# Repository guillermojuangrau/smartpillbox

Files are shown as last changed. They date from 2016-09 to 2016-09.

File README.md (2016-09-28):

# Project Title

Smart pillbox concept completed as a final project for Telecommunications Engineering Degree

## Summary of the project

Conception, design and creation of a smart pillbox (physical parts, hardware and software) as well as production of a 3D printed open-source physical wireless prototype able to automatically sort and dispense pills to dependent polymedicated patients reducing medication errors and improving medical adherence.

### Contents of the project

Project is intended to be a prototype for a smart pillbox therefore in this project there will be several subcontents regarding hardware, software or electronics.
Below there is a list of the different contents included:

1.Smart_pillbox_project_Guillermo_de_Juan.pdf - Project thesis and documentation which was presented in the final project presentation
2.Code - Code to be run in the pillbox's processor.
3.Body - Files of the 3D parts of the pillbox to be printed in 3D.
4.Schematics - Files of the schematics.

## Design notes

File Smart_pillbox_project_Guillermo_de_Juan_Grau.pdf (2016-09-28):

## ESCUELA POLITÉCNICA SUPERIOR UNIVERSIDAD CARLOS III DE MADRID

## GRADO EN INGENIERÍA EN TECNOLOGÍAS DE TELECOMUNICACIÓN

–

## DEGREE IN TELECOMMUNICATIONS TECHNOLOGY ENGINEERING

## BACHELOR THESIS – TRABAJO DE FIN DE GRADO

# SMART PILL DISPENSER FOR DEPENDENT PEOPLE

Author: Guillermo de Juan Grau Tutor: Daniel Díaz Sánchez September 2015

## ACKNOWLEDGEMENTS

In this section I would like to publicly thank everyone who has contributed in making possible for me to reach this point in my life.

To my parents, without whom I could not be the person I am today, for making me a better person since the day I was born.

To my sisters, for being always there when I need them.

To Ana, for every one of those moments in which I needed all the support and love in the world and she gave me much more than that.

To Gonzalo for those endless nights of studying, as it has finally been worth it.

To Rafa, for all he taught me the moments we spent together.

To Sara, Irene, Alicia and Dani for being the main drives of my life.

And to everyone who has helped in one or another way to make this come true.

Thank you, from the bottom of my heart.

## INDEX

6.2 | Printing software | 81
6.3 | Printing in 3D | 82
6.4 | Printed parts | 84
6.5 | Pillbox assembly and encountered problems | 86
7 | Testing the pillbox | 88
7.1 | Miscellaneous tests | 89
7.2 | Tests for the default stage | 90
7.3 | Tests for the management stage | 91
7.4 | Tests for the dispensing stage | 94
8 | Planning and budget | 96
8.1 | Planning | 96
8.2 | Budget | 99
9 | Conclusions and future work | 100
10 | References | 102
11 | Annex | 106

## CHART INDEX

## FIGURE INDEX

Figure 37: A cube is overlapped with the created part to make an entry hole in the cylinder.. 49 Figure 38: After the cube has been substracted from the cylinder the entry hole is created.... 50

Figure 48: Some of the electronic components which have been used to test and create the

Figure 50: Funduino along with the tools used to solder the necessary pins onto the board ... 57

Figure 57: Connection breadboard schematic of the speaker, LEDs, switch and button

Figure 70: Prusa i3 steel used to print the pillbox parts once assembled and functional, already

Figure 73: Example of printing a cone in a standing position and in a side position, the standing

Figure 75: Parts with the necessary quality which will be used to assemble the prototype: pill

## ABSTRACT

Many medical errors are due to the fact that people in charge of patient or elder’s medication have to deal with sorting huge amounts of pills each day. This paper consists on the conception, design and creation of a pillbox prototype intended to solve this deficiency in the medical area as it has the ability of sorting out the pills by itself as well as many other advanced features, with this device being intended to be used by hospitals or retirement homes. For the design of this device open-source based technologies will be used when possible including 3D design software and software IDE, and the prototype will be created using 3D printed plastic parts.

## 1 INTRODUCTION

### 1.1 INTRODUCTION

Medicine hasn’t always been the precise science which we know nowadays, in fact, throughout history the vast majority of maladies and afflictions would have resulted in probable death. Fortunately medicine has experienced a great development in the last century, resulting in an increased life expectancy and the possibility to cure a great quantity of diseases and health disorders.

Pills are one of the pillars of medicine, being used as direct treatments of some sort of illness as to assuring some medical condition remains stable (people with organ transplants or patients suffering from a chronic disease such as VIH).

### 1.2 PROBLEM STATEMENT

As pills have taken such an important role in everyday life there has been the past years an increase in the number of medical neglect cases related to incorrect medication given to patients, such as the case of the nurse who gave a patient a paralytic instead of an antacid that was prescribed by the doctor, causing the patient’s death [1]. After seeing so many of these cases it is evidently crucial that the correct pill is taken by the correct person at the correct time, otherwise taking an incorrect one or not taking one at all may expose the patient to several dangerous situations, ranging from mild health issues up to death.

Other cases of wrong pills being ingested by patients are caused by patients themselves, especially at an old age. As people grow old the human body tends to malfunction and the number of pills the average person has to take when certain age is reached greatly increases, were, according to a 2008 study published in the Journal of the American Medical Association, more than 40 percent of Americans age 65 and older take five medications a day [2]. Usually they are a wide range of different pills an elderly has to take at different times. Keeping track of taking the right pill at the right moment each day can become a challenging experience for the elderly, as it is not as easy as it could be for a younger person. This fact is easily explained when we understand that many of the abilities such as sight, memory or logical capabilities tend to decrease in a proportional way to age once human beings have entered old age, making it difficult for them to remember which pill to take at the correct time, remembering to take them or confusing one pill with another as the person may not be able to distinguish one from another thanks to their decreased sight as well as the similarity in the pills forms and colours. This problem will most surely be a cause for concern for the people surrounding the pill-taker, as not taking a pill at the correct time can cause severe problems (such as organ rejection in a patient with organ transplant or heart attack in patients suffering from grave heart conditions).

On the other hand several problems related to the high amount of pills nowadays are prescribed to patients are found in hospitals or in retirement homes. In these places on of the main jobs is to give out to its patient the correct pills. Managing, sorting and giving out the pills to each one of the patients can sometimes have a high chance of error, with a patient or resident receiving one or more incorrect pills.

Finally there are situation where taking an incorrect amount of pills is a matter of the patient’s inexperience and/or ignorance. No matter the cause, it has been proven that there is a significant risk of people ending up swallowing the incorrect medication or dose.

### 1.3 OBJECTIVES

The main objective of this project will be to solve the aforementioned problems by designing and synthesize a tool which will enable the owner to track every pillf to ingest in an easy and simple way requiring no training or complex learning from their side in order to operate the device. This device will be an intelligent pill dispenser.

The pill dispenser will be designed to prevent errors in hospitals and retirement homes where many pills have to be given daily to each one of the patients, each patient owning a device will not only drastically reduce the chances of errors occurring but also well optimize and speed up work for the caretakers/nurses by allowing the device to take care of pill management for them and freeing the time slot usually dedicated to that.

This device is intended to log the pill name, number of pills and hours at which each pill is actually taken versus the time it should have been taken. Nowadays there has been an increasing awareness as the number of pills prescribed to elder people, stating that so many pills may have negative effects on the patient’s health. [3] [4] The pillbox’s logs will help gather data concerning this matter.

There is a need to ensure the device is wirelessly connected so device management (defining the hours when a particular pill must be taken, number of pills in each compartment, etc…) as well as possibility of emitting warnings to the owner’s relatives or nurses if needed (such as the patient not taking pills).

In essence, the device will have to be a wireless electronic apparatus, having special attention to make it very precise as an error could prove fatal.

### 1.4 REGULATORY FRAMEWORK

The pillbox is a device which helps handling patient’s medication.For this reason the process in which to implement the pillbox in the selected organizations (mainly hospitals and retirement homes as already mentioned) will be a process similar to the one medications have to follow when being implemented in the general market.

Chart 1 shown below shows the different level through which the product will have to traverse after being implemented in public institutions. [5]

Level 1: Medication agencies EMEA (European Medicines Evaluation Agency) execute the authorization registry report in which they authorize the product commercialization based on demographic risk versus benefit study.
Level 2: The Spanish Dirección General de Farmacia y Productos Sanitarios del Ministerio de Sanidad fix the product’s Price as well as the government’s funding conditions if any.
Level 3: The Health Counselors (Consejerias de Sanidad) in each of Spain’s autonomous communities will be the ones funding the use of the product.
Level 4: Each one of the sanitary institutions will be the ones to value if the product if worth the implementation depending on the product’s value and necessity inside the institution.
Chart 1: Regulatory framework leves for a new farmaceutical drug or related

Before the product traverses through any of the levels shown in the table it will be necessary to study if the invention patented in the Spanish territory in the OEPM (Oficina Española de Patentes y Marcas) to stop any plagiarism from happening.

### 1.5 DOCUMENT STRUCTURE

In this section the structure this document follows will be detailed along with a brief explanation of each one of the different sections:

Introduction

In this section the general aims of this document is provided alongside the proposed solution and the regulatory framework which concerns the product.

State of the art

In this section different technologies similar to the one being designed are analysed as well as the different existing technologies which will help implement the pillbox.

Product design specification

This section details the different requirements and features the pillbox must possess in order to achieve successfully the aim intended in this document.

Conceptual design

In the conceptual design section an early draft of the pillbox’s behaviour is outlined as well as different draft drawings of how the pillbox could look like. These draft drawings will be later used to design the final pillbox.

Pillbox design

In this section the pillbox is designed. The pillbox functionality is divided into modules and a simplified schematic is produced. The different modules are detailed from an operational point of view and changes to the original design are also outlined. The 3D parts are designed and detailed alongside with the pillbox’s electronic circuit schematics and the code needed for the pillbox to successfully function.

Synthesizing the pillbox

This section deals on how the prototype is converted from digital to a real model. The chosen 3D technology which will be used to print the pillbox is explained along with the procedure to follow an encountered problems while achieving that.

Finally the pillbox’s creation and assembly is also covered.

Testing the pillbox

This section shows the different tests applied to the pillbox to ensure complete functionality and the changes the pillbox has to undergo to successfully pass the failed tests.

Planning and budget

This section details the planification followed for the completion of this project and the hours dedicated to each tasks as well as the necessary budget to cover the project.

Conclusions

This section covers the future improvements that could be done to the pillbox in order to optimize it and increment the number of features it presents as well as to correct errors the actual prototype possesses.

The project as a whole is reflected upon once it has been finished and the several conclusions drawn out of it are exposed.

References

The sources used and cited throughout this project are listed in this section.

Annex

Additional documentation such as high detail schematics of the printed parts are included in this section.

## 2 STATE OF THE ART

### 2.1 INTRODUCTION

Throughout this section a detailed a thorough investigation of products similar to the one developed in this project will be carried out so that a learning process is achieved in order to avoid committing common errors and flaws as well as ensuring that this project offers and outsmarts every other product in the market nowadays.

In second place the different available technologies needed for the creation of this product will be examined in order to pick the optimal ones which will be finally used to make it a reality.

### 2.2 SMART PILL BOXES

Despite the short time pill boxes have been in the market many different models can already be found with a wide range of different functionalities and intended for disparate uses and contexts. Most prominent ones will be cited.

### 2.2.1 AdhereTech’s smart pill bottle

AdhereTech smart pill bottle [6] consists on a plastic bottle in which to store the pills and some circuitry which allows for the bottle how many times the pillbox is opened. It uses sensors for a precise measurement of remaining medication and can send messages, calls or notifications to patient if pill is not taken. Its main weak points are the impossibility of storing different pill types in one bottle as well as having a lack on information on how the pillbox can be managed, which may led to believe it will only be implemented at hospital-level. On figure 1 the pillbox is shown.

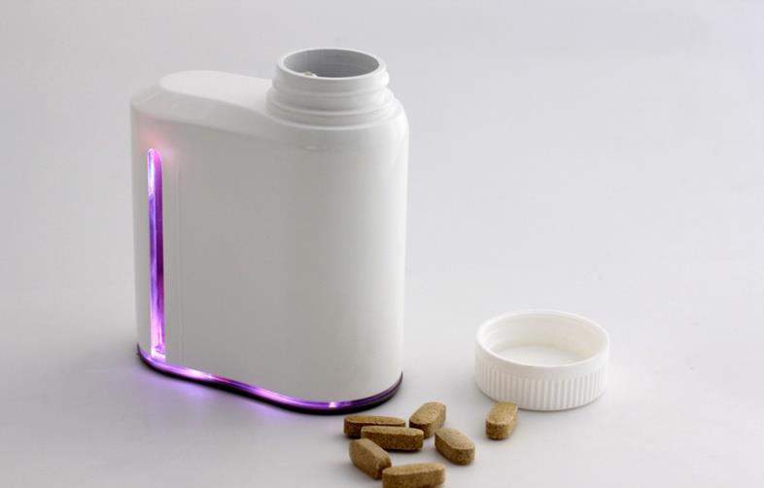
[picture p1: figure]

Figure 1: AdhereTech’s smart pill bottle

### 2.2.2 iMediPac

iMediPac [7] is an intelligent pillbox in which pills are sorted by each day in a disposable envelope which will be later inserted in the pillbox. Each day the pillbox lights up the compartment which has to be taken that day and the user breaks and retrieves the pills from inside the pillbox. If pills are not taken the pillbox alerts relatives with notifications. On the down side, the pillbox is very bulky of a huge size making it difficult for a person to carry it all day, while pills will probably have to be taken throughout the day. It also shows in the promotional videos a complex method of configuring personal data, which may lead to elderly people not being able to program it correctly. Finally it doesn’t solve the problem of pills complexity as nurses, pharmacists, etc… have to spend huge amounts of time preparing the dose for each day in the refill sheet as well as refills having to be constantly bought and refilled. Figure 2 shows the iMediPac pillbox with a refill loaded with pills.

[7]

Figure 2: iMediPac pillbox.

### 2.2.3 MemoBox

MemoBox [8] is a small pillbox with just one compartment in which many different pills can be stored. It possess a portable size and can track when the pillbox is forgotten at home. Whilst its simplicity can be very attractive it offers no more functionality than the one which could be achieved with a normal pillbox and a pill-reminder app installed in the phone. Figure 3 shows the MemoBox pillbox with different pills stored inside.

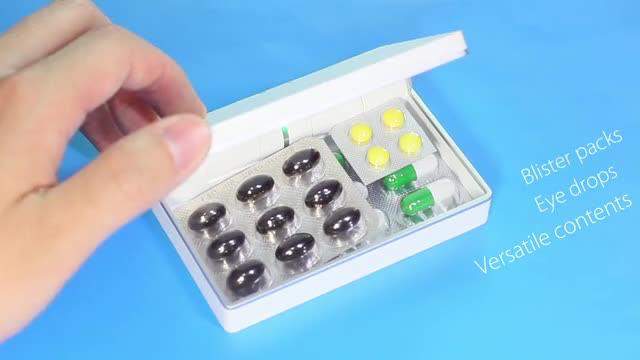
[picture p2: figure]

Figure 3: MemoBox pillbox

### 2.2.4 uBox

uBox [9] is a really small pillbox which can be easily carried by its user. It consists on a cylindrical structure with different compartments inside. It has a childproof lock and can alert user and relatives if pills are not taken. Different pills for each dose are stored in the same compartments, which may be its only inconvenient. Figure 4 is an actual photograph of the pillbox while Figure 5 shows an exploded view of the pillbox.

Figure 4: uBox pillbox

Figure 5: Exploded view of the uBox pillbox

### 2.2.5 GlowCap & GlowPacks

GlowCap [10] is a smart pillbottle lid which can attach to the normal pillbottle and comes with a wall plug device (GlowPack) which lights up each time the user has to take a pill. The pillbox lid has an interior button which can be pressed to directly order pills to the drugstore. This smart pillbox has many inconvenients:

- One cap per bottle of pills.
- Not portable as needs a wall plug-in.
- Elderly need to have computer knowledge in order to set it up.

- Pressing twice the button when pill box is near emptying places a call from your phone to the pharmacy, same thing could be achieved with speed-dial directly from the phone.
- As they are caps, only bottles of pills are allowed, not pill-boxes.

Figure 6 shows a photograph of both the GlowCap and the GlowPack.

Figure 6: GlowCap and Glowpack pillbox

### 2.2.6 MedMinder

MedMinder [11] is a huge pillbox without the possibility of being portable due to its size as well as having to be plugged into a wall outlet for it to work. Different pills go in the same compartment for each one of the pill doses, therefore not improving pill errors and for the pillbox to work it is required to pay a monthly fee. Figure 7 shows the MedMinder pillbox.

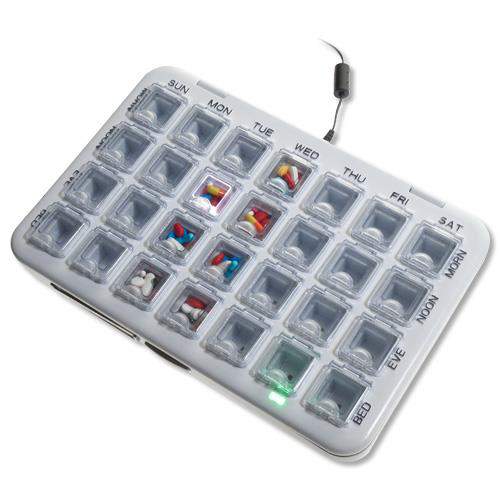
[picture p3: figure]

Figure 7: MedMinder pillbox

### 2.2.7 ePill’s Monitored MedSmart PLUS

ePill’s Monitored MedSmart PLUS [12] offers a range of automatic pill dispenser with none strong points as most of the require a monthly fee to work and are complex to operate. As well they are not portable due to their size and have an outdated style. Their elevated price also may dissuade the users to buy this pill dispenser. Figure 8 shows some of these pill dispensers.

Figure 8: ePill's Monitored MedSmart PLUS pillbox

### 2.2.8 Philips Medications Dispensing Service

Philips Medications Dispensing Service [13] is a non-portable pill dispenser oriented towards elder users which stay at home. It is operated in a very simple way with the use of one button and has voice prompts. It is equipped for emergencies with a large pill storage and a battery backup system so it can supply pills to the user in case a power outage. On its downside it is worth mentioning its non-portability and the use of individual cups with each day pills, not reducing probability of confusing pills for the caregivers. Figure 9 shows the Philips Medications Dispensing Service pillbox.

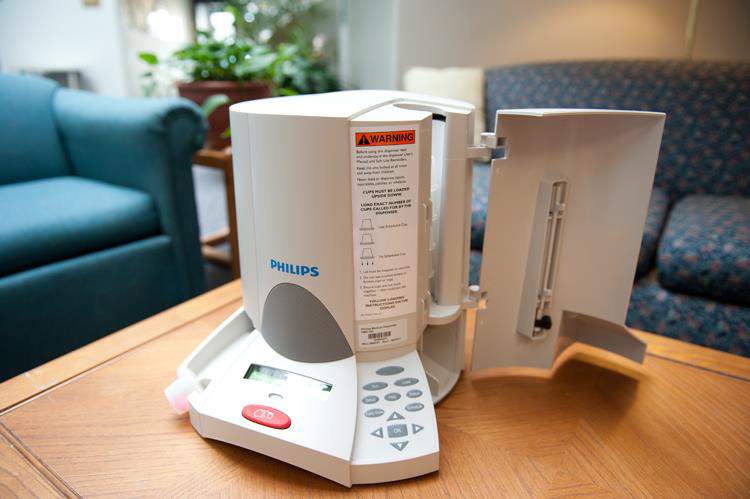
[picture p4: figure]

Figure 9: Philips Medications Dispensing Service

### 2.2.9 Conclusions

After studying the models in great detail the key strong aspects it will be necessary to focus will be:

Medication adherence

Defined as “whether patients take their medications as prescribed (eg, twice daily), as well as whether they continue to take a prescribed medication”[14] ,we are able to see that medical adherence is the key aspect the smart pillboxes focus on, as it will be the main issue, as if this is not achieved major health issues could derive.

Portability

Many of the reviewed pill boxes have to be plugged in to a power outlet, which may be a great inconvenience as it may stop medication adherence, that is due to the elderly people not constantly staying always at home, but pill remainders are constantly needed throughout the day. This will be the main reason that the project will focus on a portable device.

Simple use

Every one of the reviewed product was oriented towards elderly people, but, in contraposition, some of them expected some advanced knowledge on new technologies from the elderly people in order to configure and use the product. This is not what will be achieved in this project as it is a firm belief thatsystems have to be simple in order to be effective. Philips Medication Dispenser Service has implemented a one-button-only way for the seniors to interact and use their device, this project will focus on that aspect to create a simple to use interface in the device.

Reduction of error probability when filling the pill box

Every single one of the products in the market nowadays have different compartments at best were the pills to be taken each day are introduced, even though they may be different pill types. This does not differ in any way from the way nurses each day fill each of the patients cups with the day pills, and therefore, it is a system prone to suffering the same flaws than the ones manual systems suffer today, having equal chances of mistaking the pills and causing a medical neglect which can result even in a patient’s death.

Tracking pill intakes and safety notification systems

Tracking each time the user takes a pill and notify the patient itself and relatives will be necessary for safety reasons as well as to maintain the competitive standards if it reaches the market. This aspect will also be vital as it will provide scientific studies with decisive information and will help doctors detect medical adherence problems as well as reassuring the patient’s kin that its relative is taking its medication.

Low cost

Pillbox will need to be accessible to the general public as well as be adquired as a wholesale by hospitals and retirement homes in order for the product to succeed, therefore it will be a mandatory requisite to have a low cost price.

### 2.3 ELECTRONIC TECHNOLOGIES

All the electronical circuitry which will act as a brain of the pillbox will need to possess the following capacities:

- Sufficient processing capacity to carry out the code precise and efficiently.
- Memory enough to store code and logs generated.
- Interaction with diverse communication modules in an easy and precise way.
- Small size.
- Low price.

It has been decided that the most optimal way to implement all the electronic modules will be by using an open-source electronics platform, the best-suited candidates being:

### 2.3.1 Arduino

This platform has been a few years going round as the preferred prototyping board for small projects defined as “a microcontroller board based on the ATmega328. It has 14 digital input/output pins (of which 6 can be used as PWM outputs), 6 analog inputs, an on-board resonator, a reset button, and holes for mounting pin headers. “[15]

While a cheaper substitute would come by directly using a microchip the Arduino comes in many models making up for a preassembled expandable miniature board. Such as the Arduino Mini which can be seen in figure 10.

Figure 10: Arduino Mini

### 2.3.2 Raspberry Pi

This prototyping platform [16] is much bigger than the Arduino but comes with great processing power, as it can run a full operative system such as linux and many ports including usb and hdmi are also included. It may not be suitable for the pillbox as it has a high power consumption as well as being a big prototyping board which may not fit into the desired design inside the pillbox. Figure 11 shows the latest model available, the Raspberry Pi 2 Model B.

Figure 11: Raspberry Pi 2 Model B

### 2.3.3 The WiPy

Development board focused on developing IoT (Internet of Things) projects such as the one described by this document. Includes WiFi antenna, low power consumption all coming at a low cost [17]. This board has the most desirable features to be included in the project as it is more powerful than the Arduino board without the high power consumption the Raspberry Pi board presents as well as being very reduced in size. Figure 12 shows the WiPy board with some of its characteristic features.

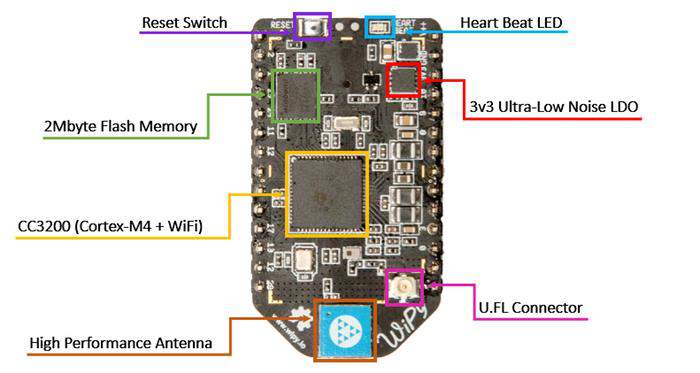
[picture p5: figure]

Figure 12: WiPy board

### 2.3.4 Conclusions

Considering the type of specifications the pillbox will have concerning portable size and wireless communications the WiPy is the best suited board for this project. Unluckily this board still is in development as it is a state-of-the-art board and access to it would mean a significant delay in the project completion.

Raspberry Pi board results in a board too big for the design and at a higher power consumption due to its excessive processing power in comparison to the one required for this project therefore the Arduino will be the selected board in order to become the pillbox’s CPU. One of its greatest advantages refers to the board being open-source, therefore many other companies can create their own Arduino boards, making it possible to acquire one with lower costs than an original Arduino board.

### 2.4 DESIGN TECHNOLOGIES

### 2.4.1 Designing the models

Modelling the physical parts which will become the main body of the pill box will need to be thoroughly designed by the help of a computerized software.

After an extensive search there was a clear need to make the production of the smart pillbox within a reasonable price, therefore a free open-source software extensively used and awarded by professionals was decided to be used. Software will be FreeCad, an Open Source parametric 3D CAD Modeler, the decisive advantage for it to be chosen being a parametric modeller, “Parametric modeling (http://en.wikipedia.org/wiki/Parametric_feature_based_modeler) allows you to easily modify your design by going back into your model history and changing its parameters. FreeCAD is open source (LGPL license) and completely modular, allowing for very advanced extension and customization.” [18]

### 2.4.2 Synthesizing the models: 3D printing

### 2.4.2.1 Introduction

3D printing is known as the technology to create a three-dimensional object mechanically based on the model of the object stored in a digital file. This process may also be referred as additive manufacturing. This denomination comes from the basic principle 3D printing uses to fabricate the object. Even though there are many different techniques to print a 3D object (different types of 3D printing will be examined thoroughly in the next section), the basic principle remains the same for all of them. This principle is based on slicing the digital 3D model into horizontal layers of very small height. The printers will be then adding layer after layer till the object is finished, with the different types of 3D printers varying only in the way layers are built.

3D printers are a state-of-the-art technology which has been exponentially reinforcing its presence within the market for the past couple of years. The popularity of this technology as well as the uses for it are also growing each day and with it the impact that it is causing in the lives of the people, as nowadays it is possible to print even a prosthetic hand (figure 13) and there are currently projects developing 3D-printed cars, houses or even organs with special printers which use biological tissue. [28]

Figure 13: Prosthetic printed hand

### 2.4.2.2 Types of 3D printing

There are many types of 3D printing techniques which may print in an extensive range of materials:

SLA

SLA refers to Stereolithography, one of the oldest 3D printing processes, patented in 1986, which starts with a vat full of photo-reactive resin in which a platform is submerged and an ultraviolet laser. The laser shines where the first layer of the model is and the resin solidifies. The platform then lowers another millimetre and the process is repeated. Parts created using this method may require the use of supporting structures which will be removed once the object is finished printing. [29]

SLS/SLM/EBM

SLS (Selective Laser Sintering) and SLM (Selective Laser Melting) are both processes similar to SLA with the difference of powder instead of liquid resin being in the vat. In SLS the laser melts the powder enough so that it fuses together but the finished part can be porous or at least its porosity may be controlled. On the other hand, SLM fully melts the powder so that it is not fused but instead it is melted into a homogeneous part. [30][31]

EBM follows the same procedure as SLM but instead of a laser being the one which melts the powder, it is an electron beam which fires electrons and the whole process usually is conducted under high temperatures of up to 1000ºC. This process is usually used to create titanium pieces and, as it is an expensive process it usually is used for bone replacements in the medical industry or in the aerospace industry.

LOM

LOM (Laminated Object Manufacturing) is a process in which adhesive-laminated paper sheets are used as the main material used to build the three-dimensional object. A sheet is rolled onto the platform and fixed by a heated roller which melts the plastic onto the platform or the layer below. A knife/laser cuts the layer of the object onto the sheet of plastic and the excess plastic layer is rolled while the platform lowers so that the next layer can be built. [32]

FDM

FDM (Fused Deposition Modeling), also called as FFF (Fused Filament Fabrication) are the same process with different names due to trademark issues (FDM is a Stratasys trademark).[33] This process extrudes melted plastic filament onto a platform layer by layer, with the plastic cooling enough to solidify once it has been fixed into the object being built. Parts created using this method may require the use of supporting structures which will be removed once the object is finished printing.

### 2.4.2.3 Conclusion

As for this project it was necessary to maintain the total production price of the pillbox as low as it could be. When reviewed it was conclusive to say that every one of the 3D printers which could be bought was well above a thousand euros. In spite of those prices, after investigation it was found out that there were people and organizations designing totally open-source 3D printers which could be built by each person in a DIY (Do-It-Yourself) fashion for a much lower price than any of the commercial 3D printers. Each one of the parts of the printer could be either bought locally in a generic shop (metal rods, rubber bands, etc…) or in an electronic shop (Arduino board, stepper motors, etc…). All the plans for building it as well as the necessary software to make it work is freely available in Internet as the whole of the 3D printer is open-source, therefore it was decided that it was mandatory to build one of these 3D printers as to finally create the pillbox’s prototype.

Throughout the following sections the history of these particular open-source 3D printers as well as the printing basics the follow and the assembly of the particular printer used to create the pillbox will be detailed.

2.4.2.4 3D printing history
This section will detail the history behind the open-source RepRap project.

RepRap project (short for Replicating Rapid-prototyper) started in the year 2005 founded by Adrian Bowyer with the idea on mind to design and create a 3D printer with an open-source philosophy of self-replication arguing that it would not be possible for the industry to create a self-replicating machine as it would never be profitable enough.

The project’s first printer was finally completed by 2008 with the name Darwin. The project gained a lot of followers and finally the RepRap Foundation was created from where 3D printed parts could be bought. Each one of the plastic parts conforming a RepRap printer can be built up by another RepRap printer. The most iconic printer was designed and finished by 2009, this printer was called Mendel and it gave birth to a new type of printer called Prusa Mendel, engineered by Josef Prusa in 2010. The Prusa printer has been the best printer which, nowadays in 2015, the best considered printers are revisions of the Prusa Mendel. This project will be using a Prusa Steel 3, which is the 3rd revision of the Prusa with a steel frame to confer more stability while printing. In spite of Prusa being the most used there is a wide range of different RepRap printers to choose from.

Zack Smith, one of the first participants in the RepRap project created the site Thingiverse, (http://www.thingiverse.com/) a platform in which anyone can freely upload the designs they create so that everyone can download them free of cost and print them if they have access to a 3D printer.

The final aim of the RepRap project is to be able to position 3D printers in households, factories and schools and universities for a very low price. The freedom of making a real tangible object from a digital model than anyone can design is believed by many in and out of the RepRap project that can cause a revolution and make a huge technological progress. [34]

2.4.2.5 3D printing basics

Filament deposition

FDM 3D printing technique feeds plastic material from a roll into an extruder which melts down the plastic and extrudes it forming each time one of the printed object’s layer. It is compulsory to calibrate the extruder’s position with respect to the printing platform as a poorly calibrated extruder can have adverse effects on the print quality. This is due to the fact that the width of the deposed plastic filament is very small and precise and the extruder needs to have enough space for the filament to exit the extruder while being pressed at the same time onto the platform (or the last printed layer) by the extruder. If not enough space is left for the filament to exit the extruder, the plastic will be forced to exit through the sides leaving an unlevelled base for the next layer whilst if there is too much space between the extruder and the platform the plastic will likely stick into the extruder and not to the platform. In section “Printing in 3D” the extruder’s calibration procedure in order to get optimal results will be detailed. Figure 14 shows the correct and incorrect positions and the likely outcome in each one of the plastic filament.

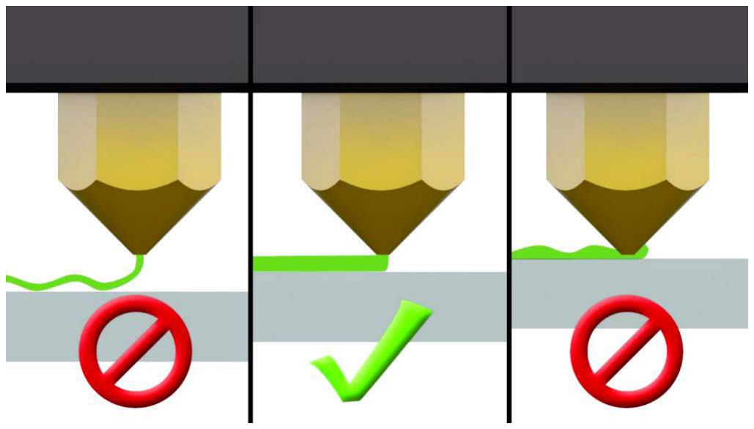
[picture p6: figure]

Figure 14: Extruder correct and incorrect positions with respect to the printing board

Types of plastic

There are different types of plastic to choose from when deciding to print using an FDM 3D printer in the market, being ABS and PLA the two most popular choices which can be bought. [34]

ABS (Acrylonitrile Butadiene Styrene) is a thermoplastic whose melting point is around 225ºC, printed parts with this material possess a great strength and flexibility. PLA (Polylactic Acid) on the other hand has a lower melting point than ABS, around 180ºC and may have some drawbacks compared with ABS, as it may be cracked more easily and glueing it together is found to be more difficult. ABS was considered at first to be the preferred option at which to print the pillbox parts but the composition of the plastic filaments was finally found to be crucial in deciding which plastic to use. ABS was found out to be petroleum-based while PLA is derived from “renewable resources, such as cornstarch, sugar cane, tapioca roots or even potato starch”. This fact not only makes PLA an environmentally friendly material to work with but, as the pillbox is intended to have medical applications, with the plastic directly in contact with the pills which will be swallowed by patients and residents, it is highly preferable to use a plant-based plastic than a petroleum-based one which could turn out to be hazardous to the human health. [35]

## 3 PRODUCT DESIGN SPECIFICATION

Product Design Specification section will define the aims the product is intended to achieve as well as the mínimum mandatory characteristics it will need to possess in order to fulfill the forementioned aims.

### 3.1 SCOPE OF THE PRODUCT

The product’s target audience are elderly people with many different pills to take throughout the week. While initially the product was designed with thinking the target audience as the main buyer of the product, it was later changed to make hospitals and retirement homes the main clients of the product, as it could increase the center’s productivity by simplifying pill management and delivery as well as giving more control and supervisión over pill intake by the center’s residents.

### 3.2 PRODUCT DESIGN

The main product consisting in a pillbox will be designed around the following principles:

- Portability, as it is much easier for the elderly to carry with them the pillbox instead of having to move each time a pill needs to be taken as well as making it easier to notice when the pillbox notifies a new dose has to be taken.
- Reasonable pill storage size, as it will not be efficient for the caregivers to refill the pillbox very frequently.
- Very clear acoustic and luminous notifications, as many elderly possess greatly diminished senses and they need to be clearly aware when the pillbox is claiming their attention for a new pill dose.
- Sturdiness so that the product’s lifespan is reasonably long while being subject to falls.
- Wireless connectivity so that caregivers may manage the device remotely
- One compartment for each one of the pill types, as this is a key aspect for highly reducing medication errors. By applying this characteristic the device is the one that manages which pills are given each day and simplifies the caregiver’s work, making more time for them to use in more pressing matters than pill-sorting.
- Ergonomic design so that both caregivers and seniors may use the device in a comfortable and safe way.
- Made with open source materials and components so that the fabrication price of each unit is reduced.
- Cheap fabrication price and low technical machinery needed so that the pillbox may be easily produced without a great investment and can be bought in great numbers by hospitals, retirement centers, etc…

### 3.3 INITIAL CONSTRAINTS OF THE PROJECT

This project will start off with some initial constraints that may need to be taken into account.

Due to the extent of this project and the multiple pill sizes available today in the market this project will assume that all pills are of one equal size due to simplicity of the project, even though the issue with different pill sizes and their inclusion in the pillbox will be accounted for in the future improvements section further on in this document. The pillbox will need a software to manage the device remotely, from an Android/iPhone app to a PC application. The development of this software is considered out of the scope of this project due to the time constraint this project has.

### 3.4 PERFORMANCE DESIGN AND ISSUES

Product size and weight

As portability is a main issue to prioritize in this product the key idea will consist on a pillbox large enough to hold a reasonable amount of pills and the necessary electronics and equipment such as batteries which allow it to function properly while being at the same time small enough for it to be handheld and making it possible for an elder person to carry it with them all day long without being a drag for the user. This last point implies it has to be lightweight accounting for the full pillbox, making it essential to be constructed fully with lightweight materials. Final size and weight will be estimated during the conceptual model section and measured in the schematical model section.

Aesthetics and ergonomic requirement

The pillbox will be designed with portability and ease of use as key aspects in mind, therefore an ergonomic design which could adapt to a senior’s hand is desired. Also, as seniors may have diminished sight one or two big coloured buttons from which the seniors can operate all the functions they need to without the use of a screen will be a feature to take into account when designing the final model.

Round or cylindrical form of the pillbox has been concluded to be optimal as it may be easier to design both the technological and mechanical inner workings of the pillbox in a cylindrical compact form as a rectangular form may result in a bigger container when trying to distribute the circuits and pill containers. In spite of that rectangular models will also be taken into account when the conceptual model is designed.

User/operator features

As the target audience for this product will be people in old age the product is required to have a very simple operating mechanism as most seniors have difficulties interacting with new technologies, therefore it is imperative that the operating mechanism is as simple as it can be, as a complicated mechanism would result in an ineffective product.

A foreseen problem the product is prone to have is the training required by the caregivers to manage and refill the pillbox. The design phase will try to work around this problem by simplifying as much as it can the pillbox management systems, but, as it is an important aspect of the pill, the product will come with a simple management and refilling program which will interactively help the caregivers through the process of refilling and managing the pillbox without no or little initial training.

Wireless connectivity is essential in the pillbox as wireless management is a key feature to simplify pillbox everyday management by the caregivers.

Performance requirements

Performance for this product will be optimized by tuning the different characteristics the pillbox ought to have regarding the environment and usage through which it will be working. The pillbox is intended to have a continuous usage, even when the pillbox is recharging or being refilled by a caregiver. Pillbox’s battery will be intended to last as much as possible taking into account size and the different internal circuits it will have to power as constraints. Battery will be fitted within the pillbox and the product will come with a charging base/cable.

Product’s shelf life will only be specified by the battery’s shelf life only in the case that comes pre-packaged with the pillbox, therefore it will be recommended to store batteries and pillboxes separately. As mentioned before, the electronic equipment and the plastic which make the pillbox can last for years in a dry safe storage.

Product service life will greatly depend on the attention and care paid by the residents when using it. To expand this service life the product will be designed so that it may prevent shock loadings such as falls and bumps using by plastic as main material which may help to absorb some shocks while being relatively cheap. Product service life will depend on the battery life also, but allowing the centre/owner to replace its battery in an easy way once the battery is becomes diminished. Also a pillbox may be reused. Pillbox in hospitals may be given to patients for the duration of their stay in the hospital, once they leave the hospital that same pillbox may be given to a new patient entering the hospital, thus allowing the hospital to work in an optimal way.

Reliability and quality requirements

Quality of the pillbox has to be assured as the service the product offers is a medical service, therefore even the smallest error could result in fatal consequences. For that reason each one of the materials of the product as well as thorough testing of each one of its working modes and safe usage will have to be conducted in order to prevent any error from happening.

Safety requirements

Product will not be completed unless all the pertaining safety tests of the product failing or bugs happening in the product’s code are passed.

In spite of the many tests, the product may still be subject to human errors (caregiver refilling the pillbox with the erroneous medication). Misuse/abuse of the product has also been taken into account as far as the scope of this project goes (residents may not access the pill compartment or let the pillbox dispense more medication than the one pre-programmed by the caregiver, but this does not prevent the caregiver programming erroneously the medication or confusing it as stated above or the resident throwing the pillbox till it breaks or using it in any other harmful way for himself or the people surrounding him).

Expected product service environment.

The pillbox will be designed to be used mainly by hospitals and retirement homes, therefore it can be concluded that no extraordinary or special conditions in temperature or pressure will be taken into account.

Plastic used by the pillbox can withstand reasonable amounts of heat, cold, pressure or humidity. The circuit components inside the pillbox can sustain a range of temperature wide enough to allow the pillbox to work normally in every condition possible inside the hospital/retirement home (Arduino microcontroller, main circuit board inside the pillbox can sustain temperatures from -30ºC up to 85ºC). The equivalent happens for humidity and pressure, no extreme conditions which alter the normal course of the pillbox will be encountered and all the circuitry will be encased tightly within the pillbox so that no dirt or similar may enter and stop the board from working.

Product maintenance and replacement requirements

The product will be designed around the idea of simplicity and reducing price not by reducing the quality of the components but by using parts which can be easily made or bought (open-source circuits and 3d printed parts) and avoiding the use of any special machinery to assemble the product. This will result in a very cheap price when a pillbox becomes broken, as replacement of the parts by the staff of the hospital/retirement homes will be impossible due to the size and distribution of the parts contained in the model.

As it is crucial that no errors occur during the product life cycle, the program intended to help the caregivers refill and program the pill dose times in the pillbox will also include a function to test each pillbox while being refilled.

Material requirements

Materials for this product will consist in plastic used by 3d printers as it will cut the production costs greatly and combined with a cylindrical shape it increases the product’s resistance against shocks, falls and bumps.

Recycling and safe disposal requirements

The designed product will be encased inside the electronic waste or e-waste. The recycling of this products will be done by the hospitals and retirement homes. Due to their nature, those organizations produce high quantities of residues of many different kinds (ranging from organic matter up to radioactive matter produced by chemotherapies as well as old electronic equipments), therefore they have special contracts with recycling plants, therefore solving the problem of recycling the pillbox as electronic waste. [19]

Manufacturing process requirements and limitations

No special measures have to be taken when manufacturing the product apart from any special limitations imposed by the different countries if necessary.

Product packaging requirements.

Packaging will consist initially in boxes made out of recycled cardboard to be as environmentally friendly as possible. The product is designed so that the hospital/retirement homes require an initial deployment by part of the producing company, therefore the packaging should be as optimal in functionality as possible, as the boxes are going to be mainly managed and operated by the producing company’s employees.

Inside the packaging the product will come in three separate parts, the main pillbox without the battery, the battery in a proper package and the charger.

Patents

In the scope used in this project, which will mainly be national grounds (Spain) the following patents need to be checked once the initial conceptual design of the pillbox is designed:

- Patent ES-1044714_U [20]
- Patent ES-1068942_U [21]
- Patent ES-1064960_U [22]

### 3.5 MARKET ISSUES

Potential customer base

Hospitals and retirement homes will be target customers to buy pillboxes to optimize the time of the nurses and caregivers in those centres. Even though those centres will be the customers the end user will be the residents and patients in need of taking pills.

Depending on the results obtained after testing and researching what is the impact and implementation in the nursing centres it may be considered to tap into seniors private homes with the pillbox in a near future.

Market constraints on the product

Main expected market constrains focus mainly on the possible size of the market, as the product deals with large hospitals and retirement homes where any change to implement may advance slowly and with many detractors against it, therefore starting small and advancing towards more greater centres once the effectivity of the pillbox has been proven by third-parties will probably be the best strategy to take.

Expected product competition

Main expected competition will be the existing one examined throughout the state-of-the-art section, which are all different model of smart pillboxes. In spite of the different models there are, their penetration in hospitals and retirement homes is actually minimum and the product being designed in this document copes with a problem any of them solves, letting the pillbox organize the pills instead of the caregiver/nurse.

Target product price and volume

While product price is expected to be reasonably low thanks to the materials and procedures used to create the product the final price will be established in the business plan section of this document, although a estimation of it being around or less 50 euros may be a prior good estimation for each unit of the product.

Expected distribution environment

Once produced, the processor will be programmed with the code, the circuitry and the physical and mechanical parts will be assembled together. Packaging box will consist in pillbox, battery and charger hold inside the box in different compartments.

Boxes will be stored till the implementation into a hospital/retirement home is required, then deployment of the pillboxes will be done via the producing company’s employees and a course for the caregivers/nurses in charge of managing the pillboxes will be offered as well as reference materials and online help, as it is vital the people in charge of refilling the pillboxes are correctly prepared.

## 4 CONCEPTUAL DESIGN

### 4.1 BEHAVIOURAL DESCRIPTION

### 4.1.1 Model description

Pillbox will work under three different working modes: user, charging or refill modes. The behaviour the pillbox will show in each of this modes will be detailed in the next subsection “Different working modes”.

Pillbox will possess the physical characteristics below:

- A big, easy to see button which will be the only one the seniors will have to use during their time as users.
- One or various LEDs to signal different working modes or notifications.
- A small simple speaker which will be used as an acoustic notifier.
- A small hole from which the pills will be dispensed at the correct time.
- One or more power/data ports from which the pillbox will be charged and some other functions may be implemented.
- Small hidden buttons for caregivers/nurses to manage the device, used to load the pill program and refill the pillbox.
- A removable cap from where to access the pill compartments, allowing for a quick and efficient refilling.
- A charger specially made to charge the pillbox.
- A program which will allow management functions for the pillbox.

### 4.1.2 Different working modes

The pillbox will possess three main working modes:

### 4.1.2.1 Normal mode

Normal mode is intended to be the default working mode when the seniors are using it. During this mode the pillbox remains in standby till a pill/dose has to be taken by the user.

Once a pill is due the pillbox will emit acoustic and visual notifications via the internal speaker and the LEDs. The notifications will last for a short amount of time which will be defined later (around 10 seconds) and then emit a bleep each 10 seconds. The LEDs will remain lit up till the senior interacts with the device and takes the pill. User will have to press the button and then the pillbox will automatically dispense the pill, shutting off all the visual and acoustic notifications once the button is pressed and the pill dispensed.

If an amount of time (to be defined in later design stages) passes without the user pressing the button the pillbox will emit a wireless notification which will alert the nurse/caregiver in charge that there is a pill pending to be taken by the user of that particular pillbox.

### 4.1.2.2 Charging mode

Charging mode will initially be similar in every possible way to normal mode for the exception of a different colour led which will be on to indicate that charging is underway.

Charging mode will only happen when the pillbox is inserted into is charging base.

### 4.1.2.3 Management mode

Management mode will be engaged when the pillbox is being managed by the management program installed on a computer. Connection will be done wirelessly.

Management program may:

- Reprogram the pillbox with the new pill schedule.
- Activate the refilling sequence, for which each of the compartments of the pillbox will become accessible while the program will indicate which pill type corresponds in each compartment so that the caregiver/nurse replenishes it.
- Run the test function throughout which the nurse/caregiver will check the correct operation of the pillbox.

Once the device enters management mode the charging LED will blink twice at the start to indicate the pillbox has established correctly the connection with the managing program.

### 4.2 PHYSICAL DESCRIPTION

### 4.2.1 Concept art & sketches of the different proposed models

Sketches for various different models were made. These sketches were merely drafts with different shapes and accessories in which the sought characteristic were implemented in different ways. Each model was sketched after a brainstorm in which the sketch was initially designed and later was drafted in a sheet of paper. A total of 5 different models were finally created.

After discarding the majority of them for obvious flaws only two sketches were taken into account as a possible starting point to start designing the first prototype of the pillbox, model A and model B, of which only one will be the one used as a starting design to create the final prototype. These two models will be analysed in the next sections, with figure 15 and figure 16 being the concept sketches of these two models.

### 4.2.1.1 Model A

### 4.2.1.2 Model B

Figure 16: Model B concept pillbox

Figure 15: Model A concept pillbox

### 4.2.2 Description of each of the models

### 4.2.2.1 Model A

Model A consists on a rectangular box design in which there are four pill compartments (labelled A to D), a big visible button in the lower right-hand side of the pillbox and a smaller switch on the lower left-hand side. Leds which indicate different working modes and notifications are located at the lower left-hand side of the pillbox, right beside the small switch. Refilling will be made by opening each one of the pill compartments at a time and when the pillbox had to dispense a pill, the mentioned pill will fall into the tray found at the lower centre in the front side of the pillbox.

Its shape was conceived thinking the idea of locating all the circuits in the back of the pillbox (circuits usually come in rectangular form, as nearly all the Arduino boards) and by seeing in a clear way how many pills were left in each of the compartments. Additionally its shape resembles those of the everyday pillboxes, which is believed to make the elders include it in their lives quicker as it is a shape they are familiar with.

### 4.2.2.2 Model B

Model B consists on a cylindrical tube with a hole in the lowest part from where it is intended for the pills to be dispensed at the indicated time. On the lower section of the tube a big button to be used by the senior users will be located and beside it the different notification LEDs as well as a smaller switch to be used by the nurse/caregiver in charge for different advanced options such as management, refilling the pillbox, etc…

On the upper section of the pillbox the different pill compartments are located, visible from the outside and are positioned around the outer rim of the section at equally spaced distances from the centre of the pillbox.

On the uppermost part of the pillbox the lid which will be used to access the pill compartments for refilling the pillbox can be found.

It was conceived in a cylindrical form as that particular form resulted more ergonomical and easier to carry for the user rather than a rectangular pillbox as well as it would simplify the inner mechanics of the pillbox by positioning the compartments around the pillbox’s outer rim in a circular way.

### 4.2.3 Conclusions

Finally became clear that the model which would continue onto the next production phase will be model B. This decision was made when an unexpected concept problem arose when studying each one of the models in further detail, which method was needed to make it possible for the pillbox to give only one pill and no more to the patients without using advanced technology which could make the both the production and the final price of the pillbox greatly rise. A purely mechanical mechanism using only plastic 3d printed parts was devised which could only be implemented in a cylindrical object and not in a rectangular (this mechanism will be examined in the ensuing sections of this document). This constraint as well as the advantages model B presented was the main motive to finally discard model A and continue the consequent phases using model B as a concept model.

### 4.3 BLOCK DIAGRAM

A simple block diagram was created to use as a template when designing the different parts (both physical and software) of the pillbox, this diagram can be seen in figure 17.

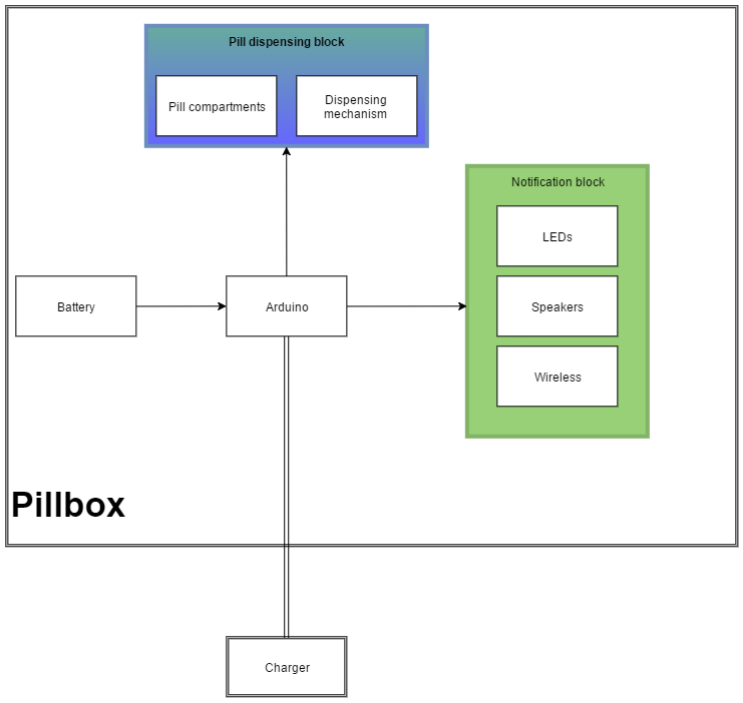
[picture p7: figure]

Figure 17: Pillbox's block diagram

Arduino board will be the “brain” of the pillbox, managing each one of the different areas and will be powered directly with the battery. The notification block will be in charge of emitting sound and light signals for the patient to know a pill has to be taken and wireless signals to the caregivers. In a separate block the pill compartments and the pill dispensing mechanism will be also managed apart by the Arduino. Finally an external charger will be in command of charge the battery directly through the Arduino.

### 4.4 PATENTS

After the creation of the conceptual design it becomes mandatory to check if there exists any patent which our conceptual design may interfere with. As stated in the Product Design Specification there are three main patents filed for a pillbox in Spain.

Patents ES-1044714_U [20] and ES-1068942_U [21] shown respectively in figure 18 and figure 19 are clear that do not interfere with the Smart pillbox designed in this document as they lack any sort of circuital device and are completely different in shape, size and functionality.

Figure 18: ES-1044714_U patent | Figure 19: ES-1068924-U patent

Patent ES-1064960_U [22] shown in figure 20 does have some resemblance as it is a circular pillbox with different compartments for pills positioned in a similar way to the pillbox being designed and has some technology which allows to notify the user when to take the pills. Although it has some points in common the pillbox being designed, it has the ability to dispense for itself the necessary pills at each moment as well as to send wireless notifications to the people nursing the pillbox’s owner. Moreover the compartments in the patent are designed to hold the different pills for a day/time of day, whilst the pillbox being designed holds in each compartment the pills of the same type and lets the pillbox sort them out at the precise time of the pill dosage.

Figure 20: ES-1064960-U patent

## 5 PILLBOX DESIGN

### 5.1 PILLBOX MODULE DISTRIBUTION SCHEME

Different modules have to be defined as stated in section “Block diagram” in the conceptual design. In order to start the final design of the pillbox it is mandatory to locate each one of the modules in a specific area. These modules will be the pill refilling mechanism, the pill dispensing mechanism and the electronic module, where most of the circuitry will be located such as the Arduino, battery, switches, etc… Also the location of the pill tray where each one of the pills will exit the pillbox must be noted in the diagram.

It has been conceived for simplicity that the outer body of the pillbox will be constructed in three different parts which will later be assembled together. Pills refilling module will be done through the lid of the pillbox, therefore its mechanism will be located in the uppermost part, pill dispensing module comprises both the mechanism needed for dispensing the pills as well as the pill storage, located in the centre part. On the lower part both the electronic module and the pill tray/hole through which the pills will be dispensed to the user will be located on the furthermost lower part, with the pill passing through the dispensing mechanism through a conduct to the pill tray.

Figure 21 represents a minimalist cross-section of the pillbox locating the modules inside the pillbox’s body.

Figure 21: Pillbox's module location scheme

### 5.2 PILL REFILLING MODULE DESIGN

### 5.2.1 Definition

This module will be in charge of allowing the person in charge of refilling the mechanism to refill adequately the pillbox with a minimal chance for errors in the process. Pillbox will only have one entry through which the pills will be introduced inside the pillbox but many different pill compartments (one for each pill type), the main function of the pill refilling module will therefore be to successfully pipe the different pills introduced in the pillbox to the correct compartment in the pill storage.

### 5.2.2 Operation

The opening will be located in the top surface of the pillbox. Refilling will be done with help of the pillbox’s management software. The person in charge will be prompted to insert a specific pill type in the pillbox and press a key in the computer when that action has been completed and the compartment for that pill has been fully replenished. Once the user hits the key in the computer the program will ask to refill another pill type and press a key and the action will be repeated until all of the pill compartments have been refilled.

### 5.2.3 Mechanism design

Pill storage will consist on a cylindrical tube where all the different compartments will be contained in the form of hollow pillars, which will be the ones holding the pills in them. In order for the pills to access each pill compartment a servo installed below the lid which will be holding the cylindrical tube will align via a command sent by the computer each one of the compartments with the entry hole, making the pills fall directly to the selected compartment. Once the compartment in use is filled the servo will rotate the tube as to align the next compartment with the entry hole.

### 5.3 PILL DISPENSING MECHANISM DESIGN

### 5.3.1 Definition

This module will take action each time a pill needs to be dispensed as it will be the module in charge of making the pill fall in the pill tray at the moment the Arduino sends the signal.

### 5.3.2 Operation

Module will need to be capable of selecting the correct compartment from the different compartments of the pill storage and it is vital it only gets one pill from the compartment, as getting more than one pill could prove fatal.

### 5.3.3 Mechanism design

The mechanism for the pill dispensing module will use two Arduino-controlled servos, one of them located under the lid and attached to the pill storage cylinder (same servo as the one used in the pill refilling mechanism) and another one which will control an intermediate piece.

Mechanism will consist in a total of four inner 3D plastic parts including the pill storage, two of them will be rotated in different positions by the servos. Diagrams will be now used to explain the different position these parts will show the mechanism extracts a pill from a selected compartment and throws it through the exit tray or chute.

Mechanism consists in three different stages: default stage, pill load stage and pill release stage. After the pill release stage the system will reset to the default stage. The system goes through the three stages each time a pill has to be dispensed to the user.

### 5.3.3.1 Parts involved in the dispensing mechanism

Parts have been labelled 1 to 4 in the following diagrams for an easier comprehension:

- Part 1 – Pill storage.
- Part 2 – Pill hatch.

- Part 3 – Pill chamber.
- Part 4 – Pill pipe.

A brief overview of these parts including simplified schematics will now be presented covering the basics needed for the reader to understand the pill dispensing mechanism. This overview will barely explain the shape of the parts as the functionality behind that shape will be covered in the next section where the three main stages for the pill dispensing mechanism will be explained. For the complete scaled schematics of these parts please refer to “Parts overview” section of this document.

5.3.3.1.1 Part 1: Pill storage
This part consists on a cylinder with hollow tunnels which cover the total length of the tube distributed radially along the tube. On the centre of the part there is a circular hole where different cables for circuits will pass when the pillbox is assembled. This compartments will be the ones storing the pills until they need to be dispensed. Each compartment will hold only pills of the same type, consequently there can be as many pill types as usable compartments minus one. This is because a compartment will always be empty and not used by the pillbox, this is further detailed in the stages overview.

A view of the part is presented in figure 22.

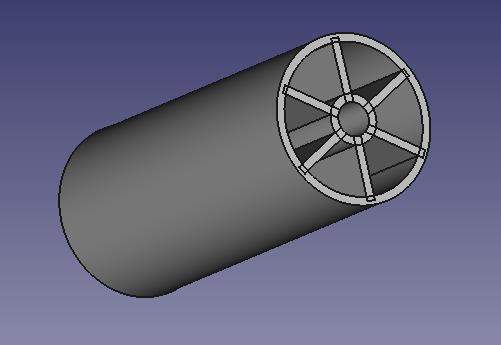
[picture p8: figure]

Figure 22: Pill storage

5.3.3.1.2 Part 2: Pill hatch
Pill hatch will be a fixed part which allows to communicate the pill storage part through a small hole with the pill chamber. It consists on a very thin circular piece with an opening big enough for a pill to pass through it and a small ramp connecting the opening to the upper level of the cylinder.

A small circular hole is located at the centre of the part designed for different cables to pass when the pillbox is assembled.

A view of the part is presented in figure 23.

Figure 23: Pill hatch

5.3.3.1.3 Part 3: Pill chamber
The pill chamber consists on a cylinder with a circular hole at the centre and another passage beside the hole. This passage is wide enough to hold a pill in an upright vertical position. The height also is the same as the model pill which will be used in this pillbox, therefore this part can only hold one pill standing in an upright position in its storage space (the storage space will be the side passage of the part, which will be also addressed as the pill chamber from now on). Part may be viewed in figure 24.

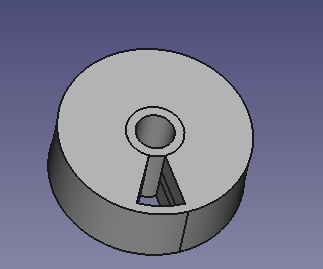
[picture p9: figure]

Figure 24: Pill chamber

5.3.3.1.4 Part 4: Pill pipe
The pill pipe part consists in a semi-circular piece with a large pipe of a considerable greater height than the circular part protruding from its side, connecting with a hole the upper part of the circular part with the end of the pipe. A semi-circular opening is also found at the centre of the circular part helping cables pass through the pillbox’s centre when it’s finally assembled. Part is shown in figure 25.

Figure 25: Pill pipe

### 5.3.3.2 Stage overview

During this overview the different stages will be presented with the help of simplified schematics which will aid in helping the reader understand the operational functioning of the pill dispensing system. The four parts will be presented in a minimalist way as seen in figure 26. During this explanation the location of the different passages will be marked in red in each of the parts (these passages will be the ones the pill has to traverse to get to the exit), as can be seen in figure 27.

Figure 26: Pillbox refilling mechanism schematic | Figure 27: Pillbox refilling schematic showing pills in the cross-section

5.3.3.2.1 Stage 1: default stage
This stage is the stage where the pillbox is by default when no pill needs dispensing, the starting position from where the pill dispensing mechanism starts.

The pill compartments in the pill storage (part 1) are positioned so that they are not aligned with the opening of the pill hatch (part 2), therefore preventing any pills to exit the pill storage.

Pill chamber (part 3) has the chamber aligned with the pill pipe (part 4), meaning it is not aligned with the opening in the pill hatch (part 2). Parts position in this stage is shown in figure 28.

Figure 28: Pillbox position of inner parts at default stage

5.3.3.2.2 Stage 2: pill load stage
In the pill loading stage both the pill storage (part 1) and the pill chamber (part 3) align with the pill hatch (part 2). It has to be noted that as the pill chamber (part 3) is aligned with the hatch then it is not aligned with the pipe in the pill pipe part (part 4). This means the chamber is closed in its lower part (preventing any pills from falling below) and open in its upper part, which connects directly to the pill storage through the pill hatch. This causes a pill to fall from the pill compartment to the pill chamber, but, as there is only space for a pill in the pill chamber, the pill itself will prevent any more pills to fall into the pill chamber. The position of the different parts is shown in figure 29.

Figure 29: Pillbox position of inner parts at pill loading stage

5.3.3.2.3 Stage 3: pill release stage
When the pillbox reaches this stage the pill chamber (part 3) will move aligning itself with the pill pipe and therefore letting the pill stored in the chamber fall through the pipe, this position is shown in figure 30. Pill storage (part 1) then rotates, aligning the empty compartment of the pill storage with the hatch opening, preventing any other compartments to be aligned over the hatch. Final position is then shown in figure 31.

Figure 30: Pillbox position of inner parts at the first step of thepill release stage

Figure 31: Pillbox position of inner parts at the last step of thepill release stage

### 5.4 CHANGES IN THE ORIGINAL DESIGN

After the start of the design certain issues have raised forcing the original design to be subject to some minor changes. These changes will be the location of the battery and the pill tray.

The battery was intended to be included besides the Arduino board with the main electronics but after a thorough search it has been decided to use a bigger battery which will allow for more autonomy, therefore having to be placed outside the main body.

The pill tray has been relocated to the side of the pillbox so that the pill has to traverse less distance from the pill storage to the pill tray, therefore preventing errors such as the pill getting stuck.

The pillbox’s new distribution is shown in figure 32.

Figure 32: Pillbox module location after revision of the original idea

### 5.5 SIMPLIFIED SCHEME

A first draft of the different parts composing the pillbox as well as some involved components such as the servos are presented in figure 33 in a simplified view of their supposed location once the pillbox is finished. This first draft alongside the different mechanisms will be used as a roadmap when designing the final models of the 3D parts.

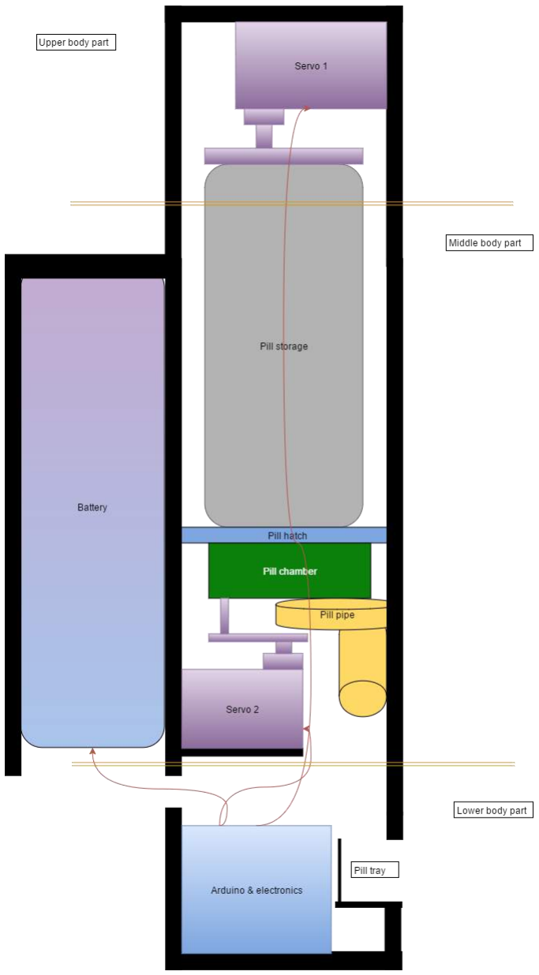
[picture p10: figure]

Figure 33: Simplified scheme of the pillbox inner part location

### 5.6 DESIGN SOFTWARE: FREECAD

The different parts will be design using an open-source software with no cost assigned to it, as it can offer a very similar functionality than other expensive programs and therefore the same results while not rising up the cost of designing and producing the pillbox. This software is the program FreeCAD [18], which is defined as a parametric 3D modeller, a program which helps to design and modify different versions of the model the user is currently working on with great ease.

Process used to design the 3D parts was to use simple shapes and make operations between them such as addition or subtraction to create the pillbox’s parts. Below a simple example is used as how the process was committed:

1. Firstly two simple cylinders are created with the desired measurements (figure 34):

Figure 34: Two simple cylinder in FreeCad software

2. The smaller shorter cylinder is positioned inside the cylinder (figure 35):

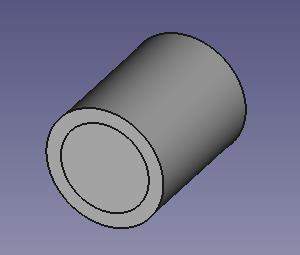
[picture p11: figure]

Figure 35: Cylinders have been positioned one inside the other

3. The smaller cylinder is subtracted from the bigger one forming a primitive version of the pillbox’s upper part (figure 36):

Figure 36: The smaller cylinder has been substracted from the wider one

4. Necessary details such as the hole from where the pills will entry the pillbox can be done using the same procedure by subtracting a cube to the created part (figure 37 and figure 38):

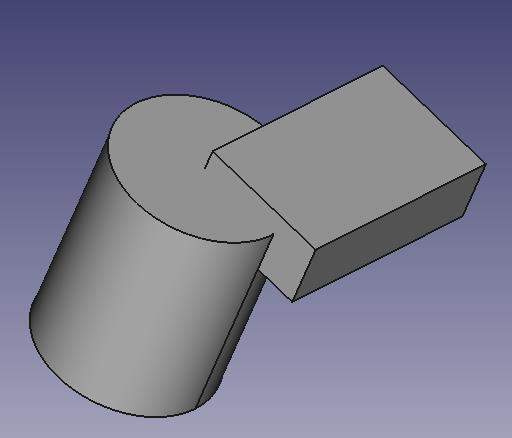
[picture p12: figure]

Figure 37: A cube is overlapped with the created part to make an entry hole in the cylinder

Figure 38: After the cube has been substracted from the cylinder the entry hole is created

Note: This example was done specifically for this section solely with explanatory purposes, as the finished parts are far more complex than the one shown in this section. Also different operations as fusing or intersecting shapes were also used for the pillbox’s design.

### 5.7 PARTS OVERVIEW

The pillbox consists on a total of 9 plastic 3D-printed parts which conform both the outer body as the inner mechanisms of the pillbox. The plans for the different parts will be shown here in a reduced scale. The actual full-size plans with measurements of each one of the parts will be appended in the annex.

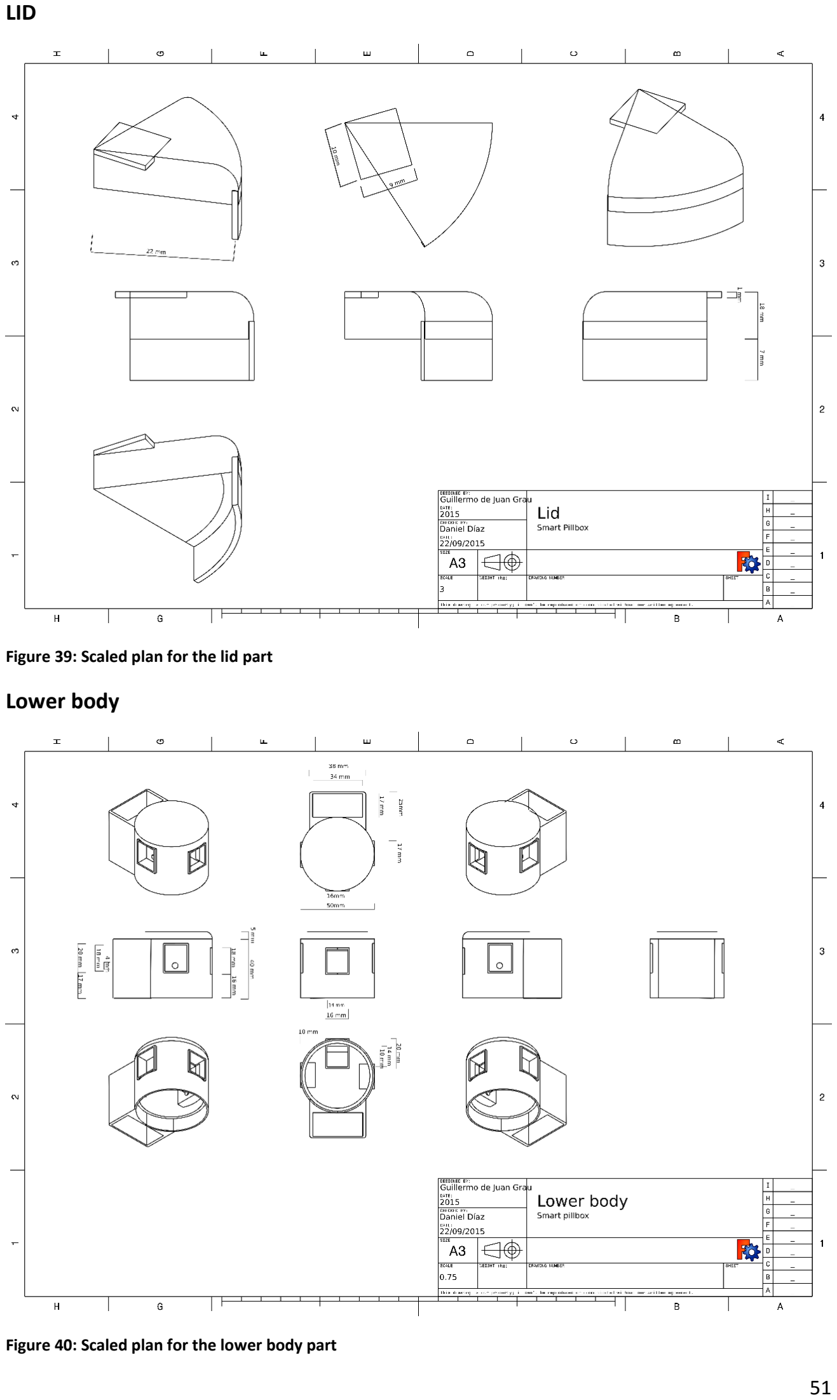
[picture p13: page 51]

LID

Figure 39: Scaled plan for the lid part

Lower body

Figure 40: Scaled plan for the lower body part

Mid-body

Figure 41: Scaled plan for the middle body partpper mid-body

Pill chamber

Figure 42: Scaled plan for the pill chamber part

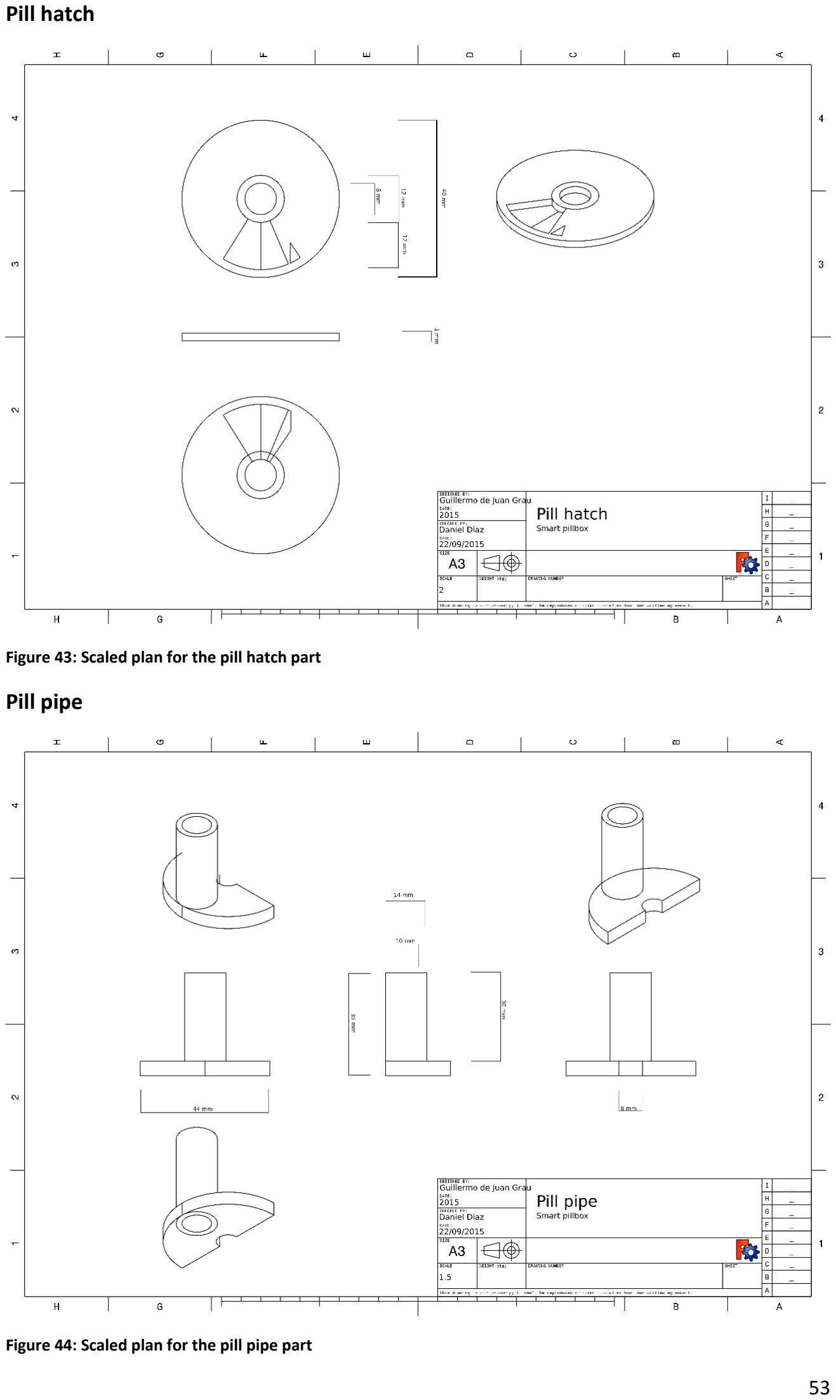
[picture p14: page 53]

Pill hatch

Figure 43: Scaled plan for the pill hatch part

Pill pipe

Figure 44: Scaled plan for the pill pipe part

Pill storage

Figure 45: Scaled plan for the pill storage part

Upper section

Figure 46: Scaled plan for the upper body part

Battery lid

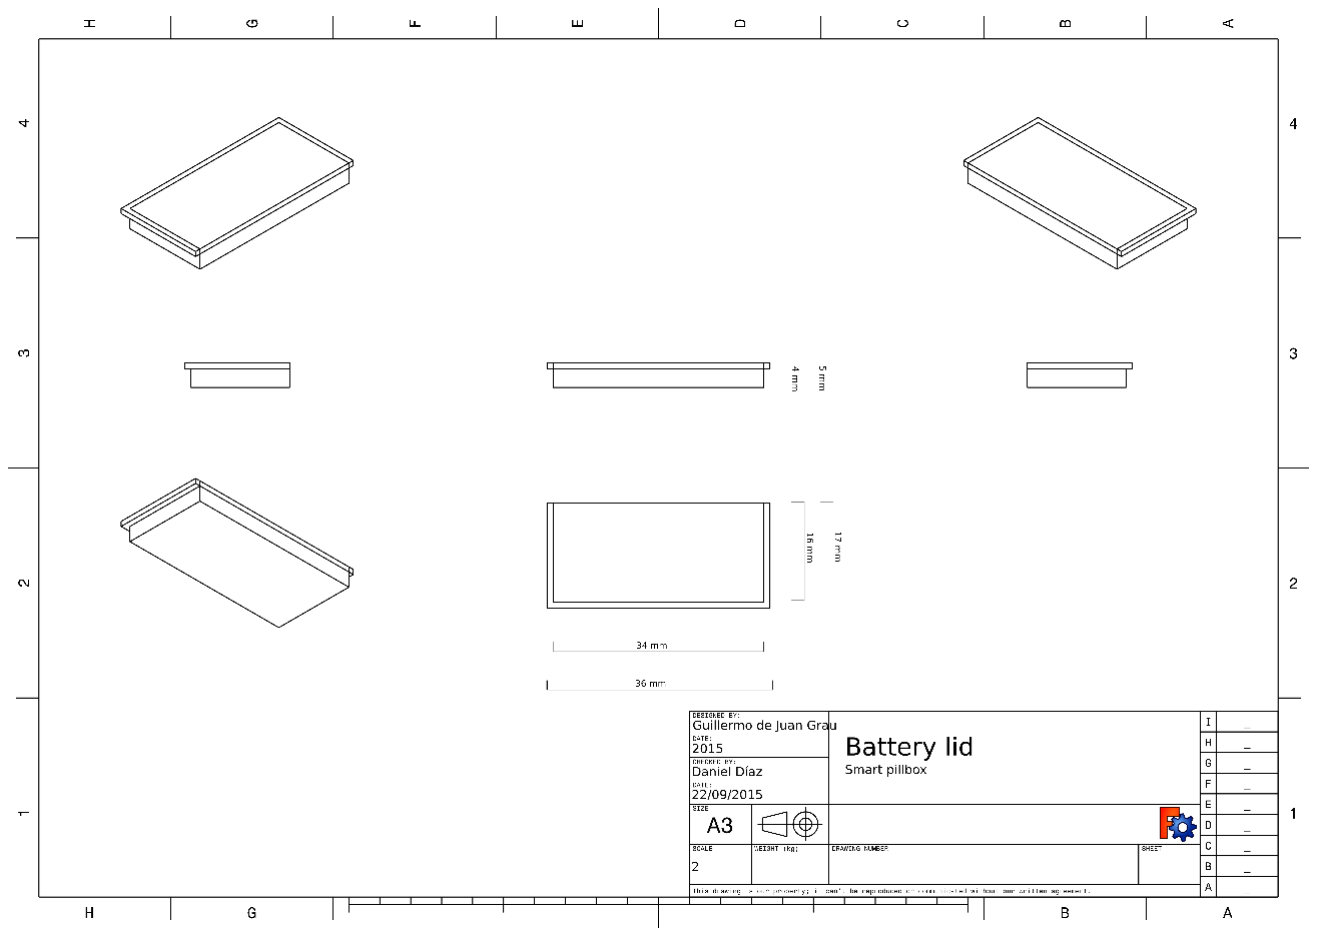
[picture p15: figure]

Figure 47: Scaled plan for the battery lid part

### 5.8 SOFTWARE AND ELECTRONICS DESIGN

### 5.8.1 Introduction and pillbox operation

A series of electronic devices will be installed inside the pillbox’s body to achieve the desired functionality of the pillbox. An overview of the selected electronic equipment will be thoroughly examined in the “Electronics overview” section while the different design steps of the software will be shown below such as the code flowchart, the pseudocode and the final code.

### 5.8.2 Electronics overview

### 5.8.2.1 Introduction

Pillbox’s internal electronics will need to perform a range of different functions, therefore a wide range of electronic modules have to be included.

In chart 2 the different functions required are shown alongside the different electronic devices which will be used to perform those functions in figure 48.

Needed functionality | Electronic device performing the functionality
Controlling the device and different electronic modules | Arduino board
Rotating inner parts of the pillbox | Servos
Light notifications | LEDs
Acoustic notifications | Speaker
Keep track of time | RTC (Real-Time Clock) module
Wireless communication | Bluetooth module
Keep logs of different pill intakes | Arduino’s EEPROM memory
Portability | External battery
Chart 2: Functionality apported by electronic device in the pillbox chart

Figure 48: Some of the electronic components which have been used to test and create the electronic circuitry

### 5.8.2.2 Arduino

Definition

Arduino is an “open-source prototyping platform”, a microcontroller-based board with various analogue and digital input/output pins and different serial communication interfaces as well as the capability to expand its functionalities by connecting external devices or circuits to the board.

The board comes with an IDE (Integrated Development Environment) which allow the user to write a code and upload it to the board.

Implementation

There is a wide range of Arduino boards in the market as well as several other companies producing copies of Arduino board (as it is totally an open-source product) which also work with Arduino IDE and cost much less than the original boards while offering the same capabilities as the original ones.

The one selected for this project will be a Funduino Pro Mini, a version of the Arduino Pro Mini which comes at a lower price offering the same functionality as the Arduino Pro Mini board. This board needs a USB to TTL serial converter to upload the code to the microcontroller as this board “comes with the minimum of components (no on-board USB or pin headers) to keep the cost down” [15], thus the CP2102 USB to TTL serial converter was adquired.

Soldering was required as the board comes without the head pins (needed for uploading the code and powering up the device) as well as pins A4 and A5 (needed for the communication with the Real Time Clock module), therefore a soldering iron and soldering wire along with some spare pins were acquired and the pins subsequently soldered in the right places. The soldered pins can be seen standing upright from the board in figure 49 and the materials used for this soldering process are shown in figure 50.

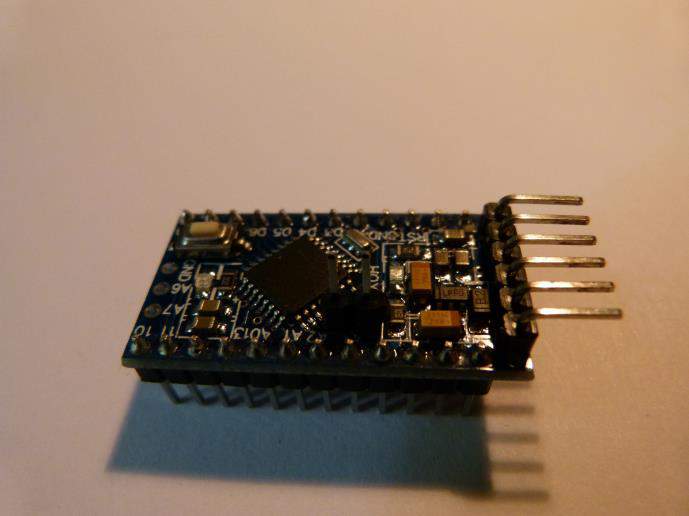
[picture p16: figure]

Figure 49: Funduino Pro Mini after soldering the necessary pins

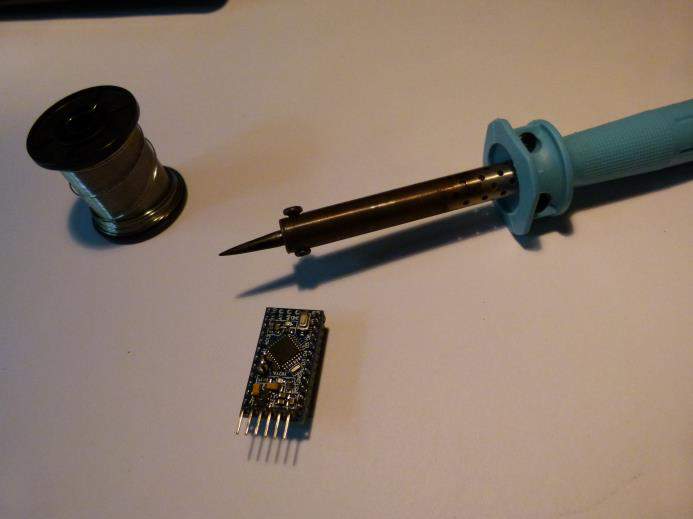
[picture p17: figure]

Figure 50: Funduino along with the tools used to solder the necessary pins onto the board

At the moment of uploading the code to the board a problem was encountered as the board did not synchronize with the computer at the time of uploading the code. After some research [15] the cause of the problem was found to be the reset pin of the board. The program which uploads the code sends a reset signal to the board when uploading the code, but the Arduino Pro Mini lacks the pin to receive the reset signal, therefore the button needs to be manually pressed in order to successfully upload the code.

A typical Arduino code consists on a file with three main blocks:

- At the top of the file all the external libraries which will be used are included with the following syntax: #include <library.h> where library.h is the library which will be included.
- setup() is a function which runs at the start of the code once and is mainly used to set up all the different variables, the pins and any other preparations.
- loop() is the main function which will be looping continuously, the main code for the program will be written inside this function.

The schematic for the Arduino connection with the PC via the USB to TTL serial converter is shown in figure 51.

Figure 51: Funduino connection schematic to the USB to TTL serial converter

### 5.8.2.3 Servos

Definition

Servo motors are electronic devices consisting on gears and a shaft which can be controlled via the microcontroller. Servo motors can adjust the position of the shaft between 0 and 180 degrees, which is done by the microcontroller sending a PWM (Pulse-Width Modulation) signal, with the width of the pulse being the factor which makes the motor turn. Minimum pulse width or duration will be around 1ms (which will make the servo turn the shaft to 0 degrees) and 2ms (which will make the servo turn the shaft to 180 degrees) on most of the small servos to be used with Arduino boards.

Servos will be needed to control the rotation of the pill storage and pill chamber parts so that pill refilling and pill dispensing mechanism can work correctly.

Implementation

Two servos SG90 were adquired for this project. These servos are quite small in size (22.2 x 11.8 x 31 mm) and weight (9 grams) which suits them perfectly for the pillbox as keeping both size and weight to a minimal value was a priority.

SG90 servos come with three cables, two are for power supply (Vcc and ground), which will be connected directly to the Arduino 5V and Gnd pins respectively and a third cable which will be connected to a PWM ouput pin of the Arduino. There are some digital pins which are capable to send PWM signals in the Arduino, in the case of the Arduino Pro Mini these pins are D3, D5, D6,

D9, D10 and D11, a servo can also be attached to any of the analogue pins as it can also work with them. The connection are shown in figure 52.

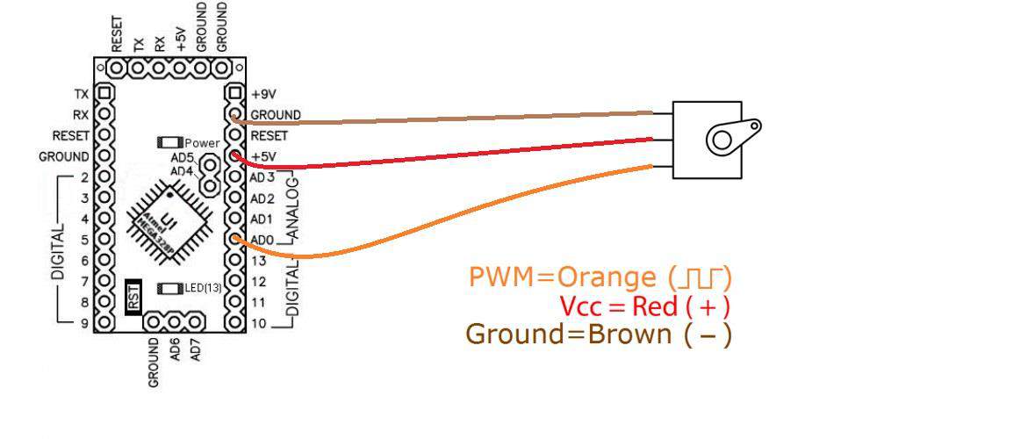
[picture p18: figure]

Figure 52: Servo connection schematic to the Funduino board

For the use of servos in Arduino the following steps are to be followed:

1) Include library Servo.h at the top of the code: #include<Servo.h>
2) Create an instance of Servo: Servo myservo;
3) In the setup() function it is necessary to attach the servo to a pin: myservo.attach(PINNUMBER); where PINNUMBER is the number of the pin in the Arduino board and myservo is the servo object we created in step 2.
4) In loop() function the servo can be controlled using myservo.write(pos) where pos is a number between 0 and 180 which will be the degree number that the servo must rotate its shaft.

### 5.8.2.4 Bluetooth module

Definition

Bluetooth is a “telecommunications industry specification that describes how mobile phones, computers, and personal digital assistants (PDAs) can be easily interconnected using a short-range wireless connection.”[23] Therefore Bluetooth is a wireless technology which enables two devices using this technology to communicate in a fast and secure way. “Bluetooth technology operates in the unlicensed industrial, scientific and medical (ISM) band at 2.4 to 2.485 GHz, using a spread spectrum, frequency hopping, full-duplex signal at a nominal rate of 1600 hops/sec. [24]

There are 3 different types of Bluetooth, Class 1, Class 2 and Class 3. Class 1 has a connection range of about 1m, Class 2 can handle connections up to 10m and Class 3, mainly used for industrial purposes, can handle connections up to 100m. Class 2 Bluetooth is the most commonly used Bluetooth and the one which will be implemented in this project. This type of Bluetooth has a very low power consumption of about 2.5mW.

Implementation

There are many Arduino-compatible Bluetooth device in the market due to its popularity in a wide spectrum of prices. The first option that was considered was to acquire the official Arduino Bluetooth shield.

This module had three main drawbacks, it was overprized (around 25 euros) and its size, as it was bigger than the Arduino board itself and lastly it took up many of the pins of the Arduino board only for Bluetooth. For those reasons the Arduino Bluetooth Shield was discarded and a small unofficial Bluetooth module was selected. This module works by using the serial communications of the Arduino board, costs around 10 euros and can be seen in figure 53.

Bluetooth module has 4 pins, 2 for powering the device (which will be connected to Vcc and Gnd pins of the Arduino board), one for receiving data from the Arduino board and sending it via Bluetooth and another one for transmitting the data received from Bluetooth to the Arduino board. Connections are shown in figure 54.

Figure 53: Bluetooth module acquired for this project

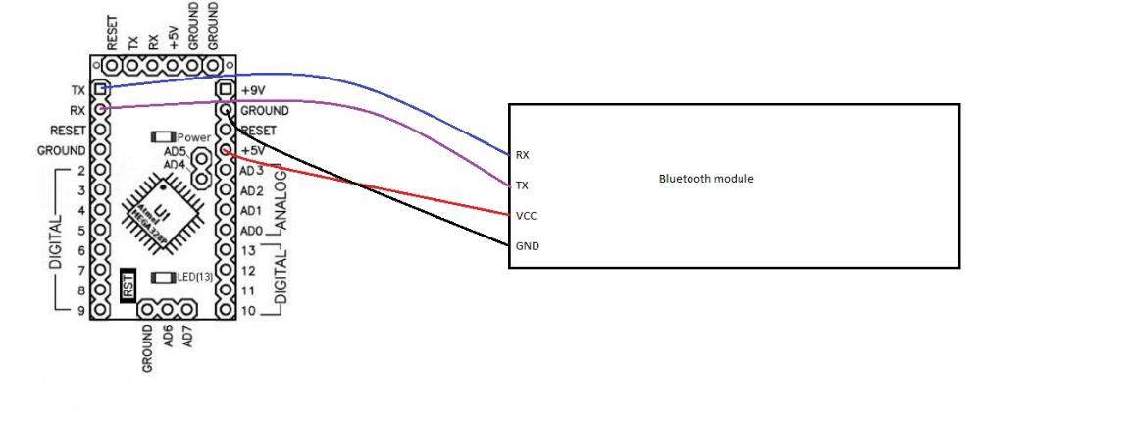
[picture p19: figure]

Figure 54: Bluetooth module connection schematic to the Funduino board

Code for managing the Bluetooth communications are done via the serial port of the Arduino:

1) First, the serial communications must be started at a already defined baud rate which can be handled by the Bluetooth module, this is done with the following code: Serial.begin(BAUD_RATE); where BAUD_RATE will likely be 9600 bps.
2) To read data received it is necessary to check if there is data available to read with the code: Serial.available() if there is any data to read it can be recovered with received_data = Serial.read();
3) Sending data via Bluetooth can be done with code Serial.println(STRING_TO_SEND);

In order for communication to happen the device communicating with the pillbox must have paired with it previously. Pairing is a process in which two Bluetooth devices establish communication with a preassigned password, typically 0000 which is the case of the Bluetooth module used in the pillbox.

### 5.8.2.5 RTC (Real-Time Clock) Module

Definition

Real-Time Clock [25] are usually referred to tiny circuits which form part of a bigger circuit but have their own power source (commonly a coin cell,a CMOS battery). This circuit is in charge of tracking the time even when the bigger circuit to which they are attached is powered off. This type of circuits are found in computers, laptops, etc… so that the operative system knows what time is it when the user powers on the computer. Figure 55 shows the RTC module acquired for this project which is described in the implementation section below.

Figure 55: RTC module acquired for this project

Implementation

The pillbox may not always be switched on and while the Arduino has an internal clock, it only takes track of the time from the exact moment de Arduino is powered on, thus lacking the track of what hour and day it is in the week, which becomes a mandatory requisite for tracking when the pills have to be dispensed to patients.

An RTC module was acquired, a Tiny RTC Module which communicates with the Arduino board via I2C communications. I2C communications (Inter-Integrated Circuit) communication protocol
[26] which allow the RTC module to communicate with the Arduino. I2C will use to cables attached in each of the components to the SCL pin (through which a clock signal will be transferred to synchronize the data) and the SDA pin (Serial Data Line through which the data will actually be transferred). These connections are illustrated in figure 56.

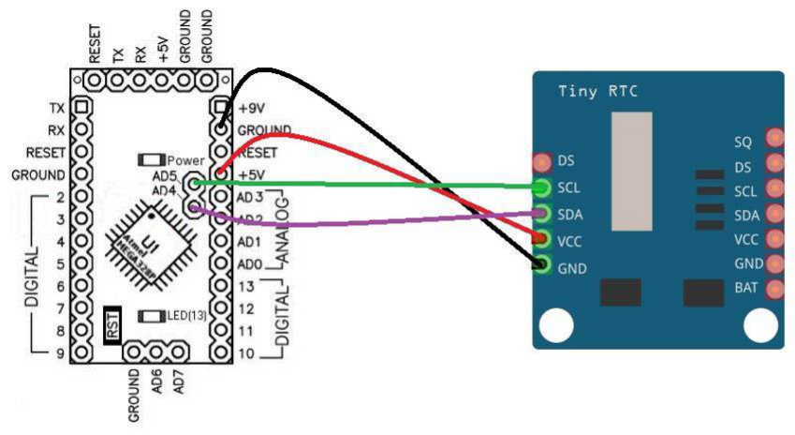
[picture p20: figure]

Figure 56: RTC connection schematic with the Funduino board

To control this software:

1) It is mandatory to include default libraries <Wire.h> and the specific library for the module <RTClib.h> which has been downloaded from GitHub (https://github.com/adafruit/RTClib) [39] and define which module will be used with the line RTC_DS1307 RTC;
2) It is necessary to start both the Wire (the I2C communication) and the RTC module with Wire.begin() and RTC.begin()
3) The time can now be instantiated with DateTime now = RTC.now(); and be accessed with several functions: now.hour(); now.day(); now.month(); now.year(); now.seond(); now.dayOfWeek();

The module can be programmed with the correct time using RTC.adjust(DateTime(__DATE__, __TIME__));

which sets the time of the module at the time the program was compiled. This line will not be inserted into the final code as it would cause the module to reset its internal clock each time the pillbox was switched on. The module will be pre-programmed with the correct time before being inserted in the pillbox’s circuitry.

### 5.8.2.6 EEPROM MEMORY

Definition

EEPROM (Electrically Erasable Programmable Read-Only Memory) is a non-volatile memory which comes with each one of the Arduino boards.

Non-volatile memory stays when the device is powered off and this will be needed to store the pill schedule information, this is, each one of the times in a week the pillbox will dispense a pill and which pill type is the one dispensed.

It is mandatory to store the pill schedule in non-volatile memory as the device may be powered off in some occasions, thus making it essential for the pillbox to retain the pill schedule in a non-volatile memory so that it may resume functioning properly once turned on again.

Implementation

EEPROM memory in the Arduino model this project uses (Arduino Pro Mini) has 1kB of memory. A single entry in the pill schedule will take up a total of four bytes in memory as will be shown in chart 3.

Byte number | 1 | 2 | 3 | 4
Information stored | Day of week | Hour | Minute | Pill type
Possible values | Monday/Tuesday/Wedn esday/Thursday/Friday/ Saturday/Sunday | 0-23 | 0-59 | A/B/C

Chart 3: Byte map for a single pill dose stored in memory

The day of the week in which the pill will have to be taken will be stored in the first byte, the hour of the day in the second, the minute in the third byte and the last byte will be reserved to specify which one of the pill compartments the pill will have to be taken out of.

A table will be done to map the different values of each of the fields into a number which will be written as a byte in the eeprom memory. As the information will be stored in separate bytes it was considered to write the byte number which directly corresponded to the value being written (e.g. if the pill dose had to be on Friday at 5:05 then the value 5 would be written in byte 1 corresponding to the fifth day of the week, value 5 would also be written in bytes 2 and 3 corresponding to the fifth hour and the fifth minute within the hour) but was decided to map each one of the values into different values to prevent errors from happening when reading from the memory.

Day of the week:

Chart 4 shows the number mapping each day of the week.

Day of the week | Monday | Tuesday | Wednesday | Thursday | Friday | Saturday | Sunday
Number | 2 | 3 | 4 | 5 | 6 | 7 | 8
Chart 4: Day of the week value mapping to a byte value

Hour of the day:

The hour of day will be a number from 0 to 23 and will be mapped subsequently from numbers 9 to 33. The possible values for the hour will be 9≤X≤33, therefore X-9 = hour at which the pill will need to be dispensed.

Minute:

Minutes will be mapped in the range of numbers from 34 to 94, consequently

34≤Y≤94, where Y-34 will be the formula to find the minute at which the pill has to be dispensed.

Pill type:

There are three possible pill types, A, B and C which can be dispensed by the pillbox, the mappings are shown in chart 5.

Pill type | A | B | C
Number | 95 | 96 | 97
Chart 5: Pill type mapping to a numerical byte value

The number 1 will be written as the last byte when there are no more pill doses to be read from the memory as an EOF character. Each time a value is read from the EEPROM memory a check to see if the value of the number is within the expected range of numbers for the byte that has been read.

As the EEPROM memory can hold 1024 bytes and each entry in the pill schedule takes 4 bytes then the memory could hold up to 256 entries in the weekly pill schedule, a number which will be enough for the common user of the pillbox.

To operate with the EEPROM memory the library EEPROM.h has to be included in the code with the line #include <EEPROM.h> then the memory can be accessed with different functions such as EEPROM.write(a,b) which writes byte b in address a of the memory or EEPROM.read(a) which reads the value at the address a.

### 5.8.2.7 Switch, button, LEDs and speaker

Definition

Switch

A switch will be used for accessing the managing options of the pillbox. If the switched is in the ON position a LED will be lit up and indicating the pillbox is in Bluetooth mode, with the nurse or caregiver in charge of managing the pillbox prepared to access the pillbox’s management options.

Button

A push button will be used in the board to activate the dispensing procedure. When a pill is pending to be dispensed the button will be pressed by the user and the pillbox will be dispensed.

LEDs

Leds will be used to notify if the pillbox is in management state and to notify the user that a pill is pending to be dispensed.

Piezospeaker

A piezospeaker will be used to notify with an acoustic notification that a pill is pending to be dispensed till five minutes have passed or the user presses the dispensing button

Implementation

The piezospeaker will be connected directly to an output pin and can be controlled through the code with the tone function: tone(pin_number, frequency_of_tone, time_to_play);

The LEDs and the switches and buttons will be connected with 220 ohms resistors to output or input pins depending on the function they will be executing (refer to Pin Mapping section in this document).

The breadboard view in figure 57 and the schematic in figure 58 show how the connections with these components will be made.

Figure 57: Connection breadboard schematic of the speaker, LEDs, switch and button components

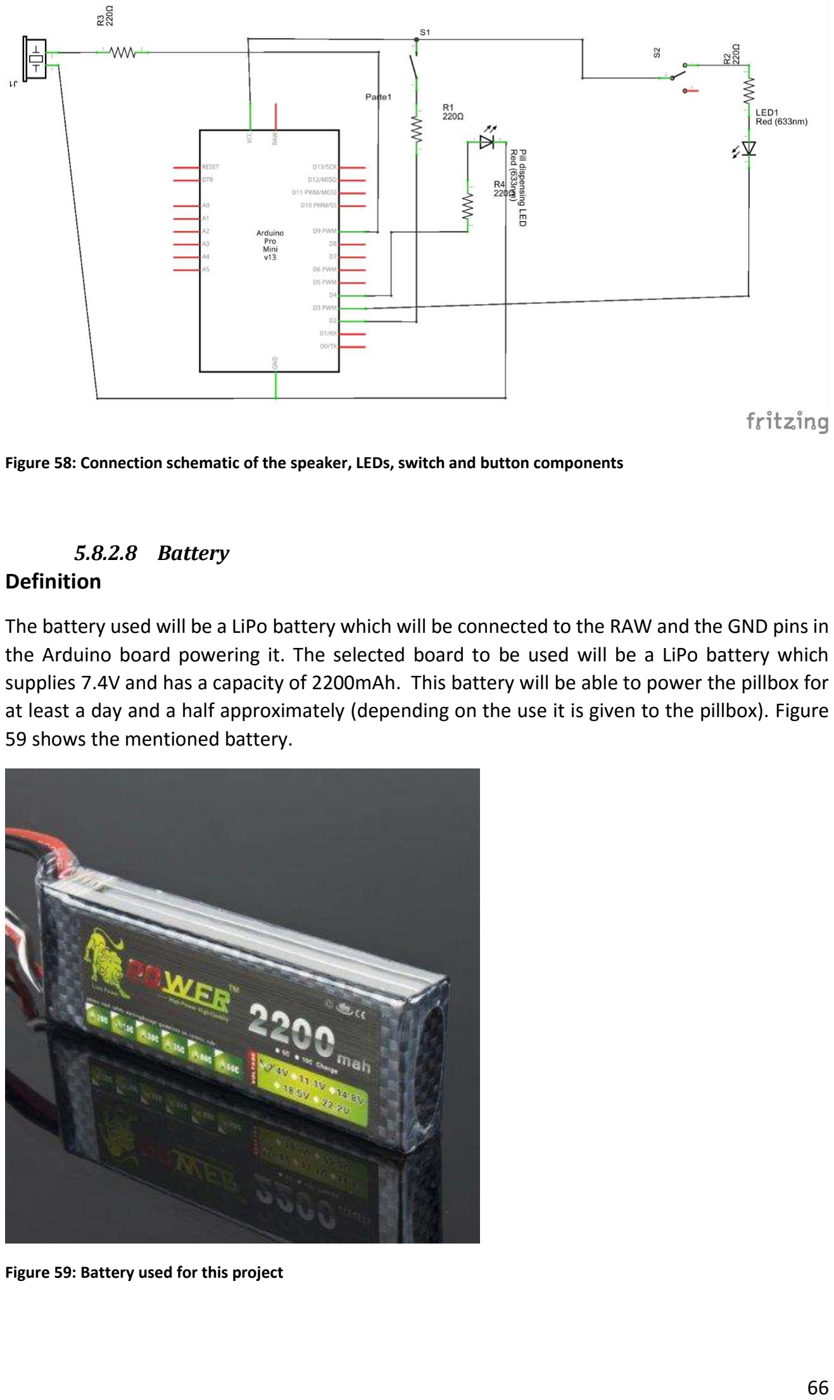
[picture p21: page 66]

Figure 58: Connection schematic of the speaker, LEDs, switch and button components

### 5.8.2.8 Battery

Definition

The battery used will be a LiPo battery which will be connected to the RAW and the GND pins in the Arduino board powering it. The selected board to be used will be a LiPo battery which supplies 7.4V and has a capacity of 2200mAh. This battery will be able to power the pillbox for at least a day and a half approximately (depending on the use it is given to the pillbox). Figure 59 shows the mentioned battery.

Figure 59: Battery used for this project

Implementation

As the pillbox will be acquired by an organization (hospital or retirement home) the company will supply with the number of pillboxes a greater number of batteries for the pillbox as well as a number of LiPo chargers. These chargers (figure 61) will be able to charge the pillbox’s spare batteriesthe retirement home/hospital has while the patients are using the pillboxes using other batteries. Once the batteries of one of the pillboxes start to run out it will be changed by one of the caregivers/nurses and the empty battery will be put to charge. As the pillbox hasn’t been implemented with a battery measuring device the pillboxes will also be sent with lipo voltage check circuits (figure 60) so that the nurses/caregivers will be able to monitor the voltage level of the battery when it is running low.

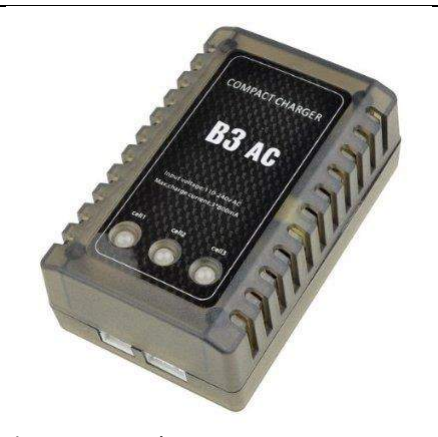
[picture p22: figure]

Figure 60: Voltage checker component | Figure 61: Battery charger

### 5.8.3 Electronic schematics

### 5.8.3.1 Designing the schematics: Fritzing

Fritzing is defined in their web page as “an open-source hardware initiative that makes electronics accessible as a creative material for anyone”.[27] This software allows its users to create easy schematics in various different designs, with a breadboard view were the circuits are implemented with a prototyping breadboard aide, the proper schematical view and an alternative PCB view were the circuit implemented in the schematic view is automatically calculated and produced as it would be if it was implemented in a PCB.

### 5.8.3.2 Pin mapping

Chart 6 shows the different digital pins to which the different components will be connected and if those pins will be in output (sending signals to the devices) or input (receiving signals from the devices).

Connected part | Arduino pin number | Input/output pin
Servos | D5 and D6 (PWM) | Output
Button | D2 | Input
BT switch and LED | D3 | Input
Dispensing LED | D4 | Output
Speaker | D9 | Output
Chart 6: Pin mapping chart

### 5.8.3.3 Breadboard and PCB schematic

The first step to créate the final schematic was to design a breadboard view in which the connections could be made with the help of a breadboard. Figure 62 shows this breadboard connection scheme. Afterwards the program used (Fritzing) was able to design a PCB version of the circuit which can be seen in figure 63.

Figure 62: Breadboard connection schematic of the pillbox circuitry

Figure 63: PCB schematic of the pillbox circuitry

69

### 5.8.3.4 Final schematic

While the PCB version shown in figure 63 was produced automatically by the program the final schematic of the connections had to be drawn manually. Figure 64 shows this final schematic version with all the connections are clearly shown and marked.

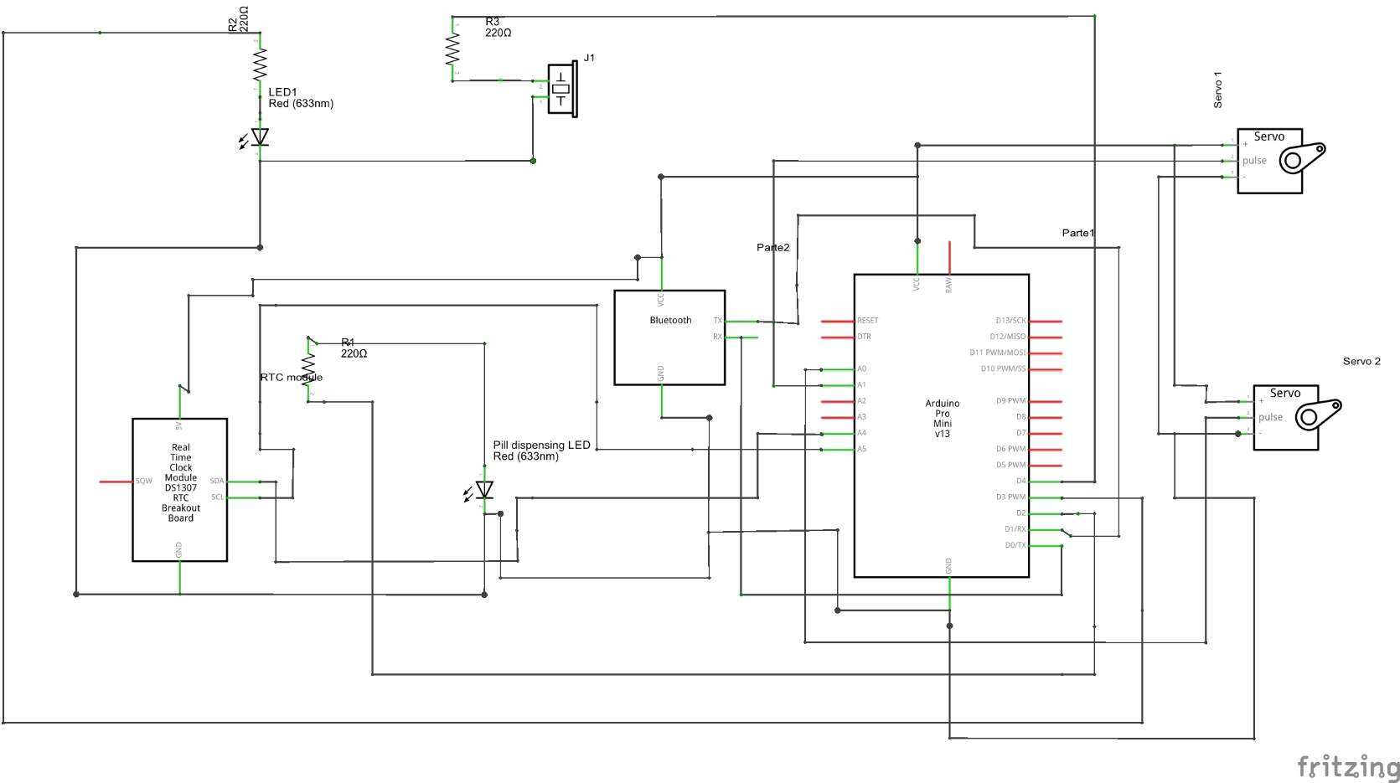
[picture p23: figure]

Figure 64: Pillbox circuitry schematic

### 5.8.4 Code flowchart

A flowchart was the first step needed to create the final version of the code. This flowchart would represent the logic of the pillbox when operating. Although the flowchart is the starting point of designing the code the functionality of the final code may vary. Figure 65 shows the flowchart.

Figure 65: Code flowchart

### 5.8.5 Pseudocode

In this section the code’s pseudocode is shown in Chart 7. Pseudocode consists on a readable versión of what the code will be and it has been based on the flowchart shown in figure 65. The final code will be programmed basing on the pseudocode shown here.

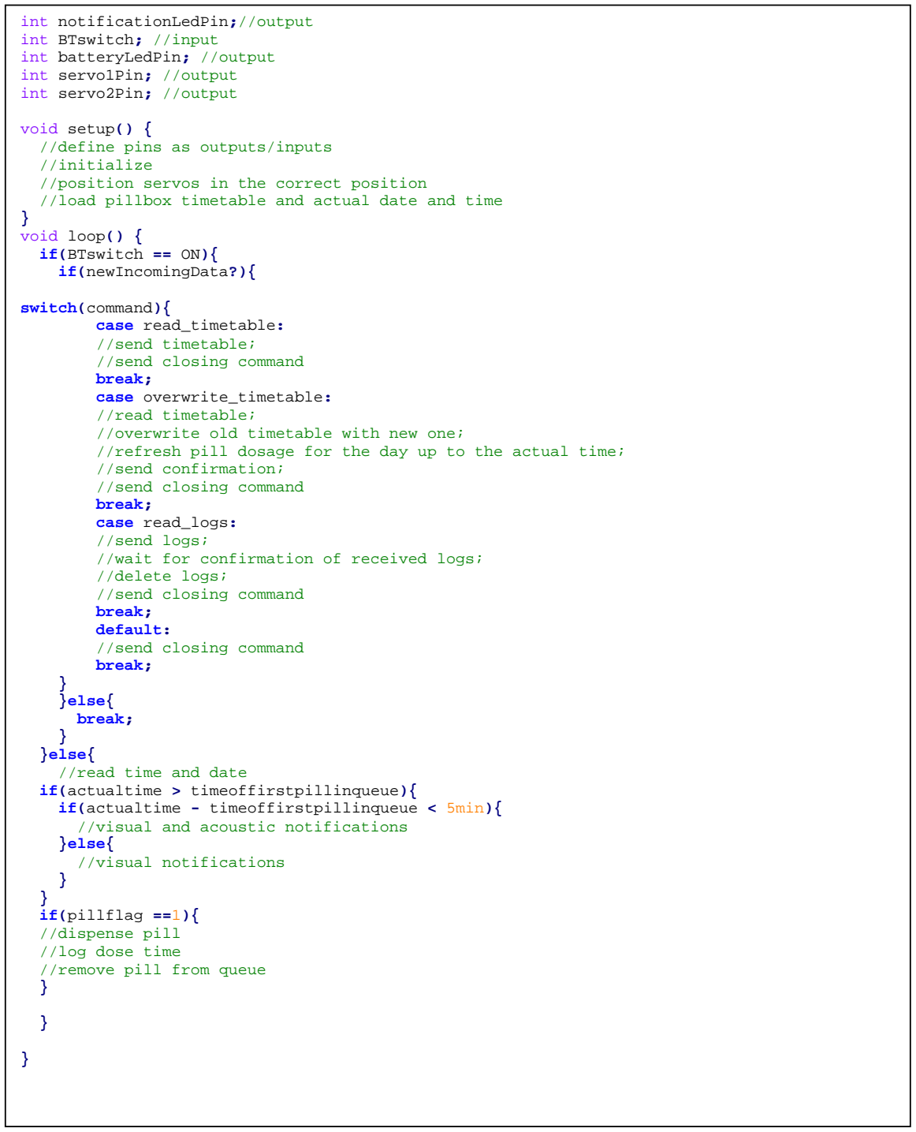
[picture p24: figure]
int notificationLedPin;//output int BTswitch; //input int batteryLedPin; //output int servo1Pin; //output int servo2Pin; //output; void setup() { //define pins as outputs/inputs //initialize; } void loop() { if(BTswitch == ON){ if(newIncomingData?){; switch(command){ case read_timetable: //send timetable; //send closing command break; case overwrite_timetable: //read timetable; //overwrite old timetable with new one;; //send confirmation; //send closing command break; case read_logs: //send logs;; //delete logs; //send closing command break; default: //send closing command break;; } }else{ break;; } }else{ //read time and date; //visual and acoustic notifications }else{ //visual notifications; } if(pillflag ==1){ //dispense pill //log dose time //remove pill from queue }

Chart 7: Pseudocode

//position servos in the correct position //load pillbox timetable and actual date and time

//refresh pill dosage for the day up to the actual time;

//wait for confirmation of received logs;

if(actualtime > timeoffirstpillinqueue){ if(actualtime - timeoffirstpillinqueue < 5min){
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

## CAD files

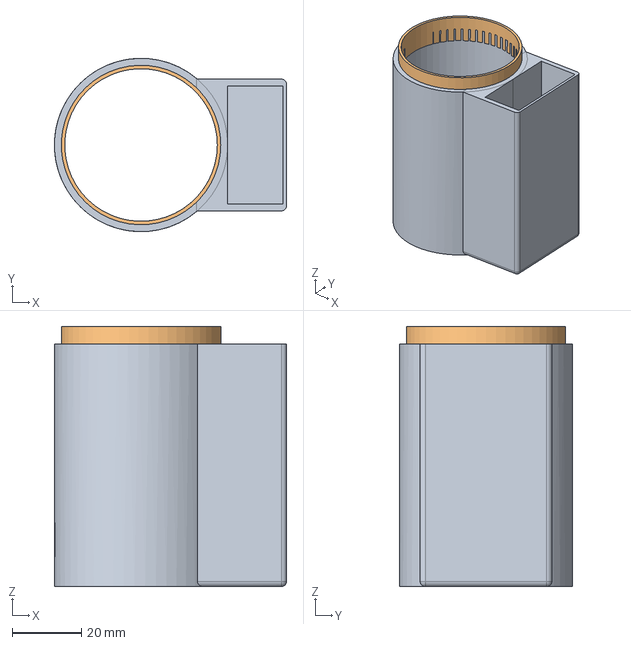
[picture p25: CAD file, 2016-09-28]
Body/Mid section.FCStd
67.0 x 50.0 x 75.0 mm

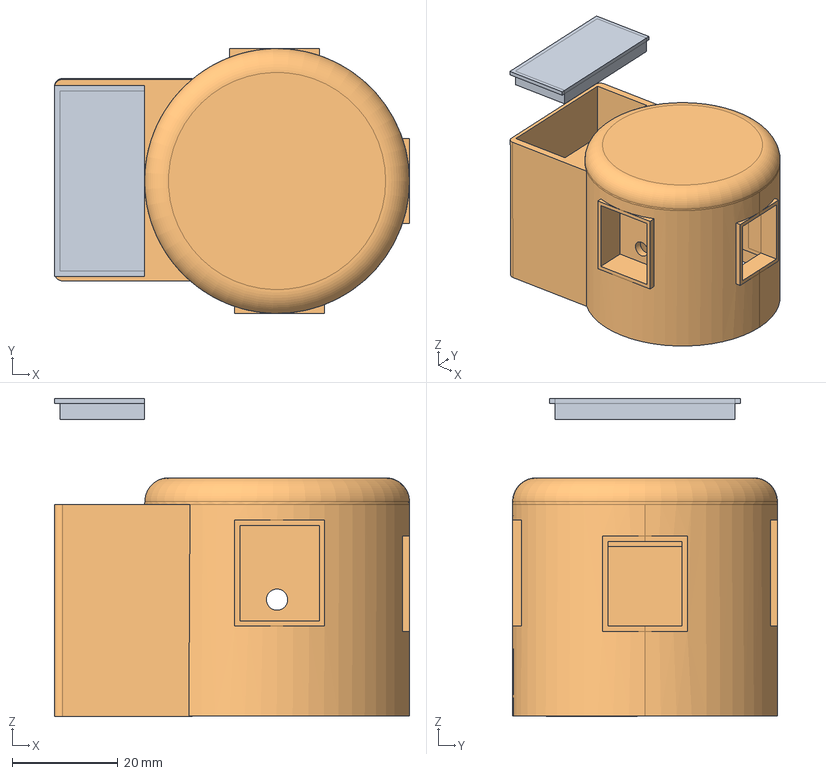
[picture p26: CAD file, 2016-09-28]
Body/Lower section.FCStd
67.0 x 50.0 x 60.1 mm

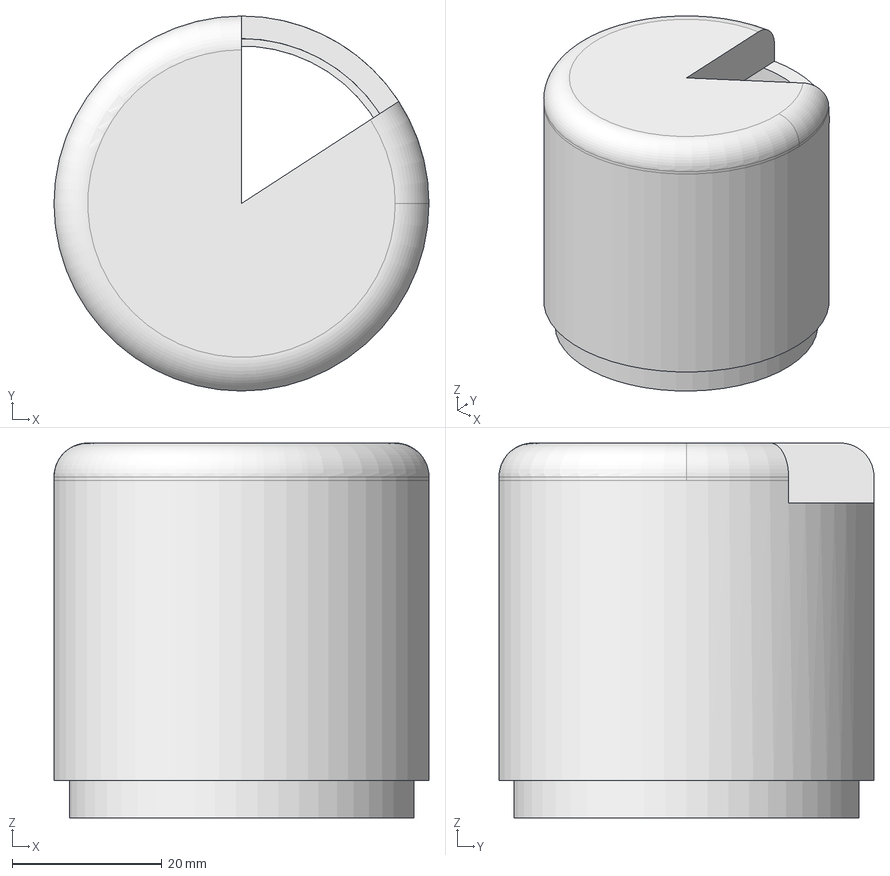
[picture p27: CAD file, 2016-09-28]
Body/Upper section.FCStd
50.0 x 50.0 x 50.0 mm

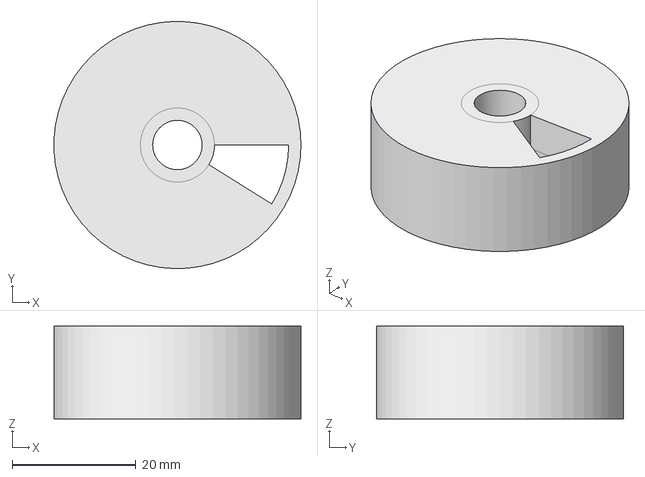
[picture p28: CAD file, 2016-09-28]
Body/Pill chamber.FCStd
40.0 x 40.0 x 15.0 mm

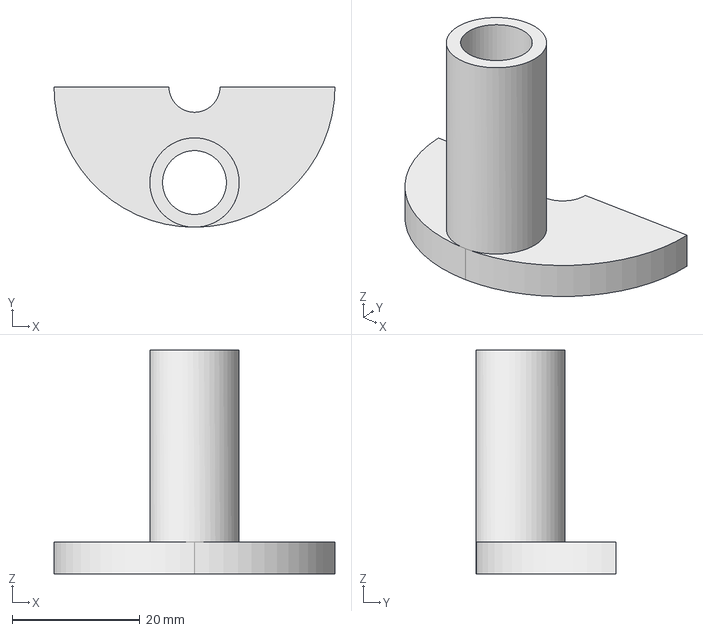
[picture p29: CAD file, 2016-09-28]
Body/Pill pipe.FCStd
44.0 x 22.0 x 35.0 mm

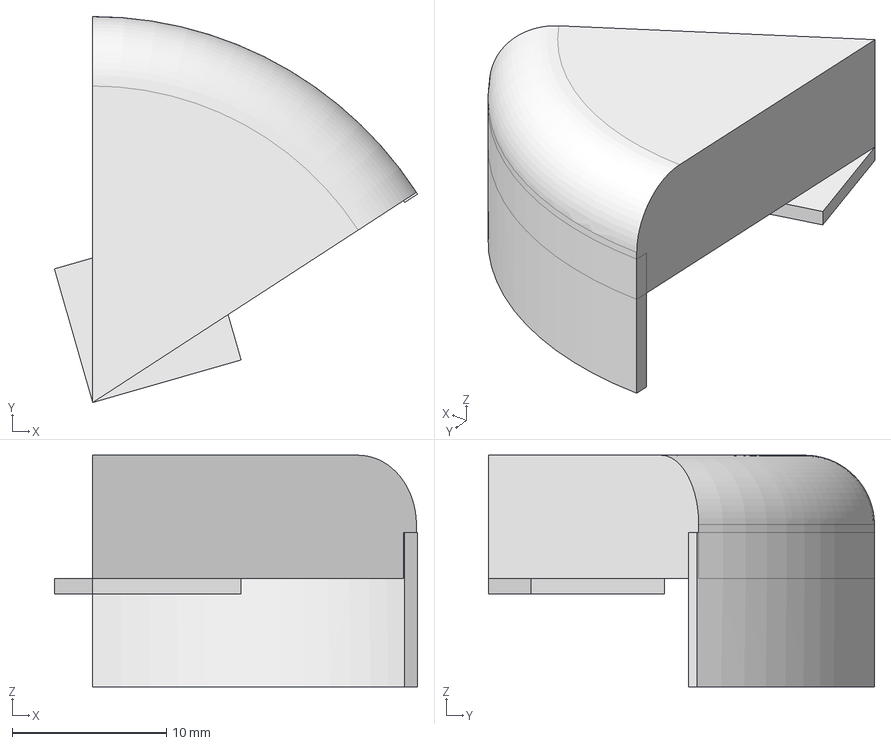
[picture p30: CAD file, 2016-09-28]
Body/Lid.FCStd
23.5 x 25.0 x 15.0 mm

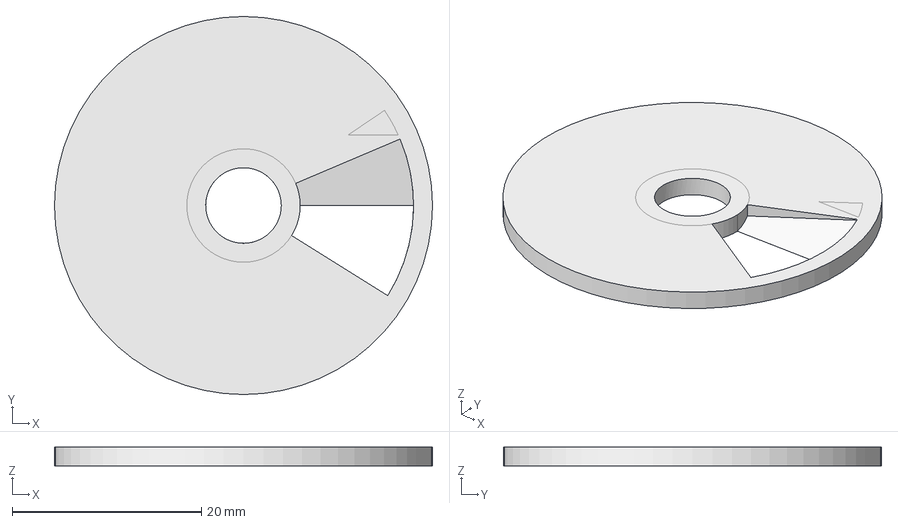
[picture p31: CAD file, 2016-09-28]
Body/Pill hatch.FCStd
40.0 x 40.0 x 2.00 mm

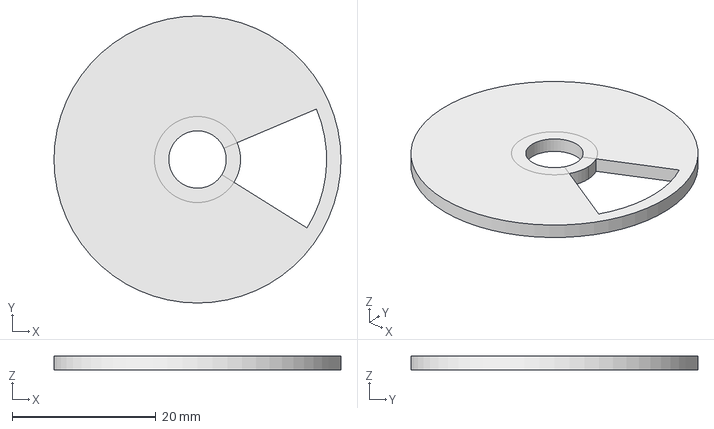
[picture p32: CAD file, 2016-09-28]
Body/Pieza no usada.FCStd
40.0 x 40.0 x 2.00 mm

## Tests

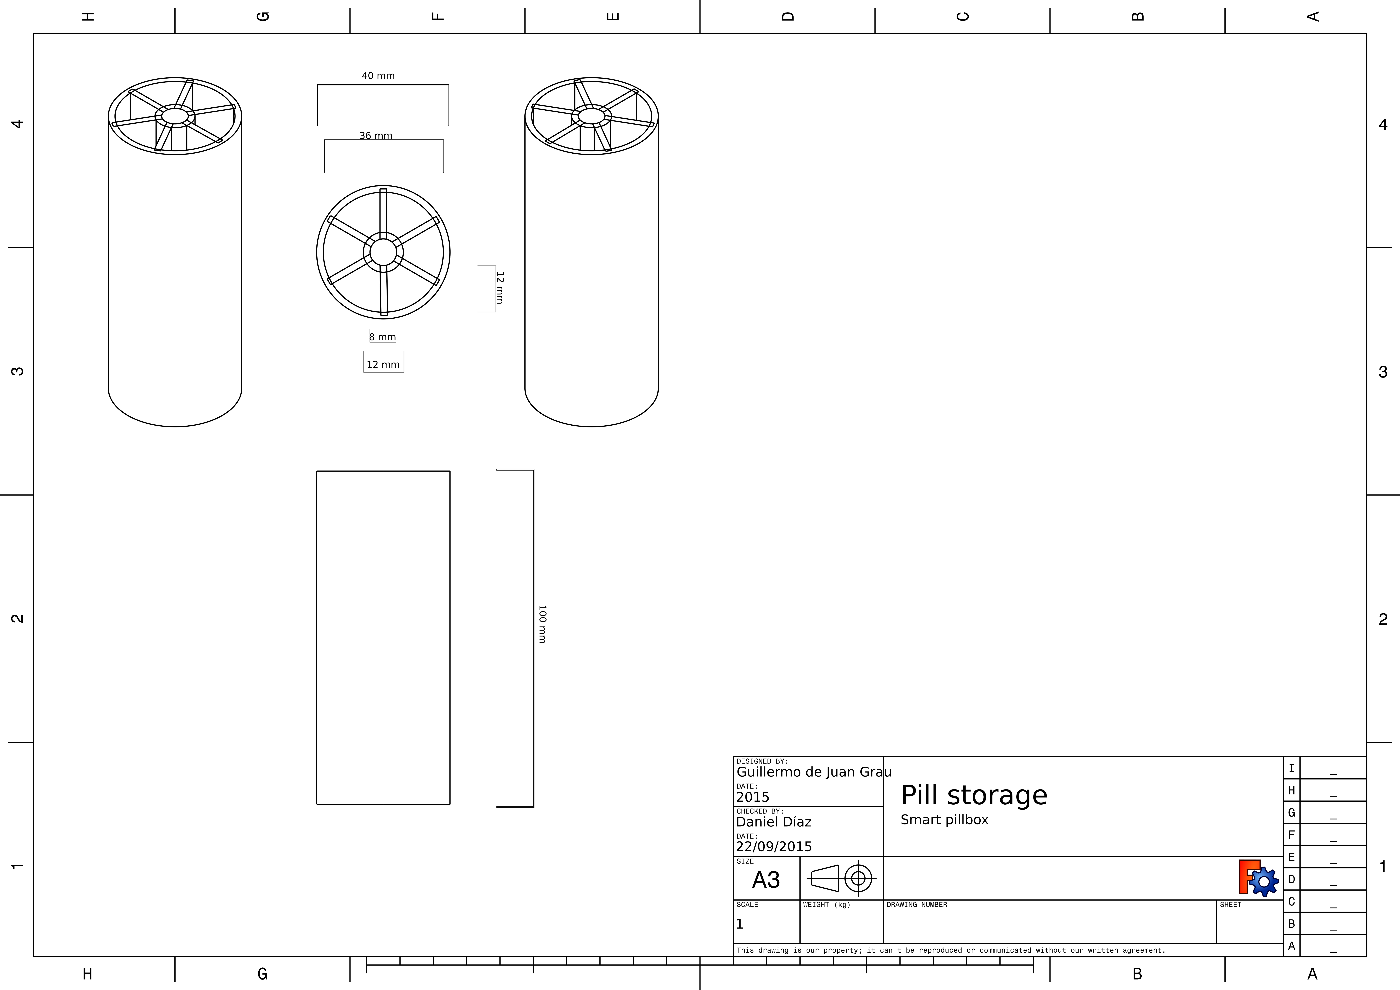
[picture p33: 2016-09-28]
Body/Measured blueprints/Pill storage2.png

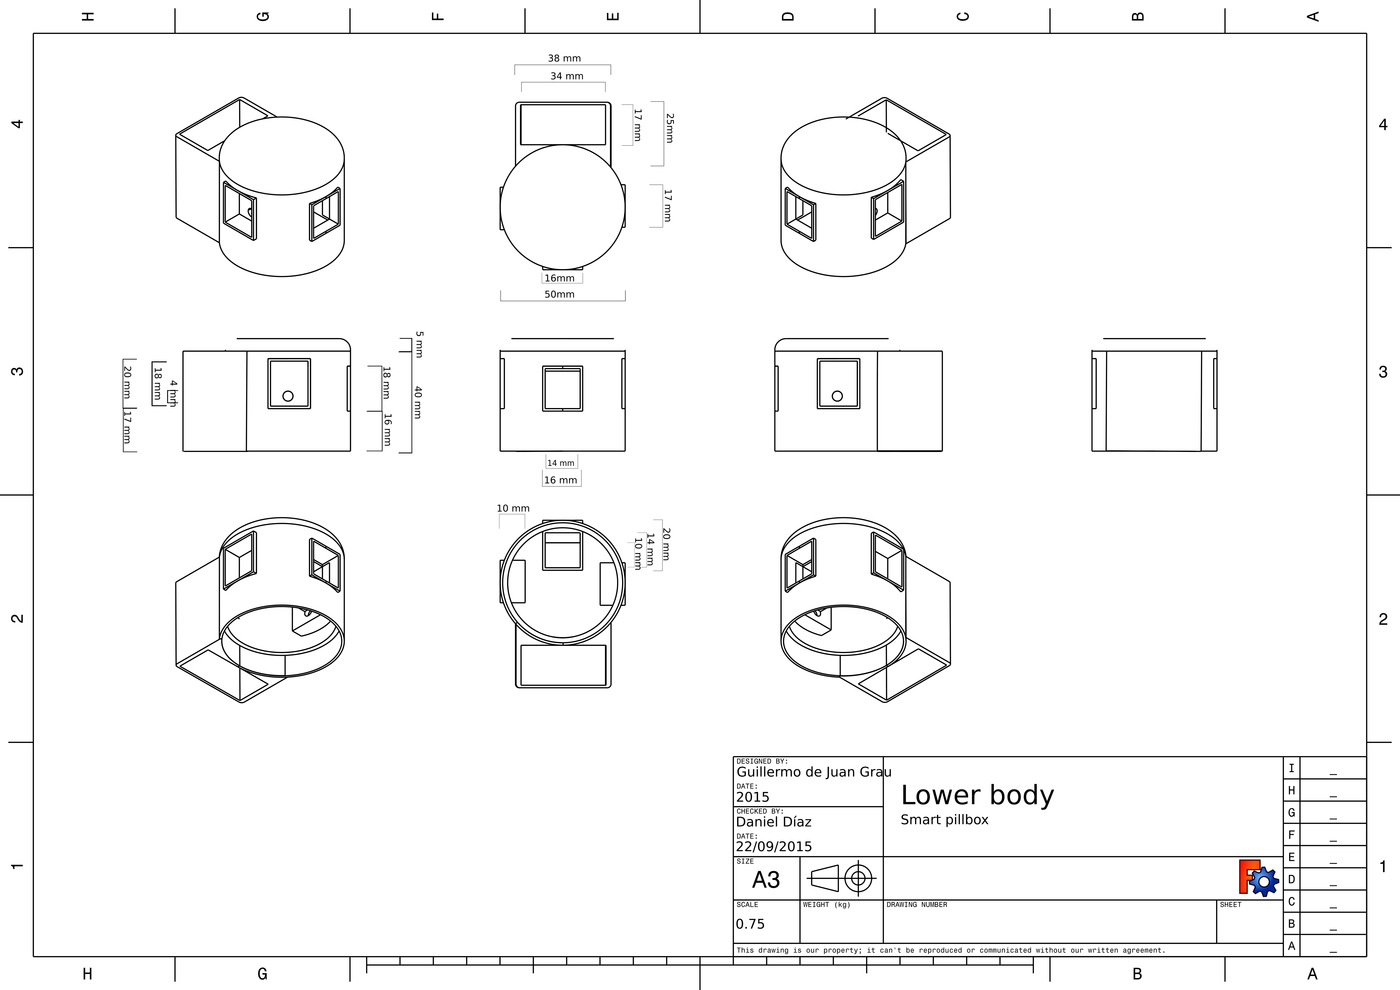
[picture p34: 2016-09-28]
Body/Measured blueprints/Lower body2.png

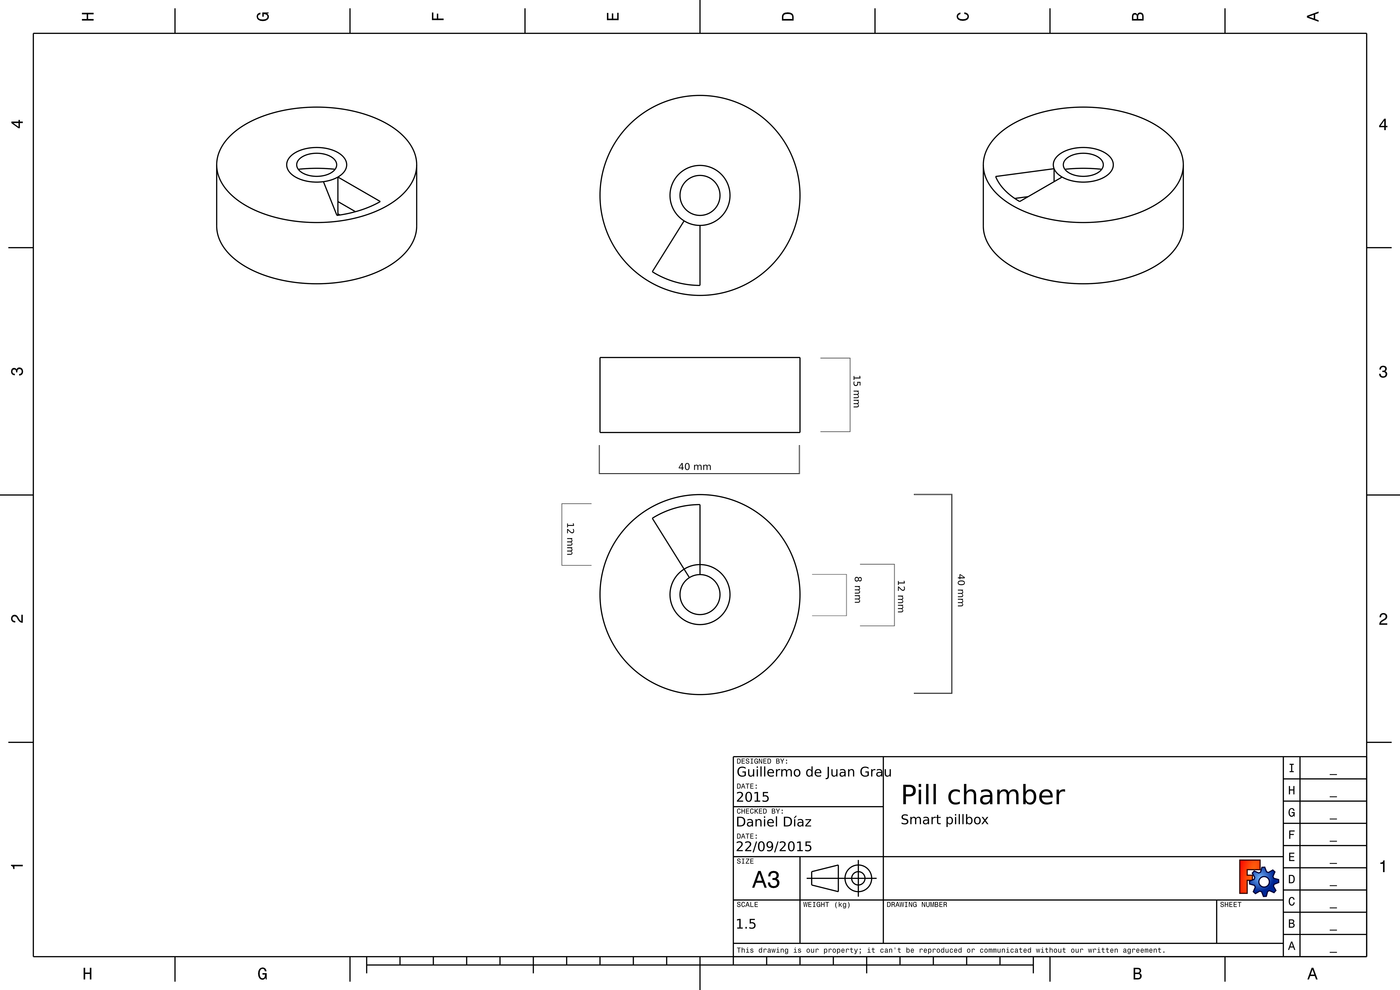
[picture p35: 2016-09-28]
Body/Measured blueprints/Pill chamber2.png

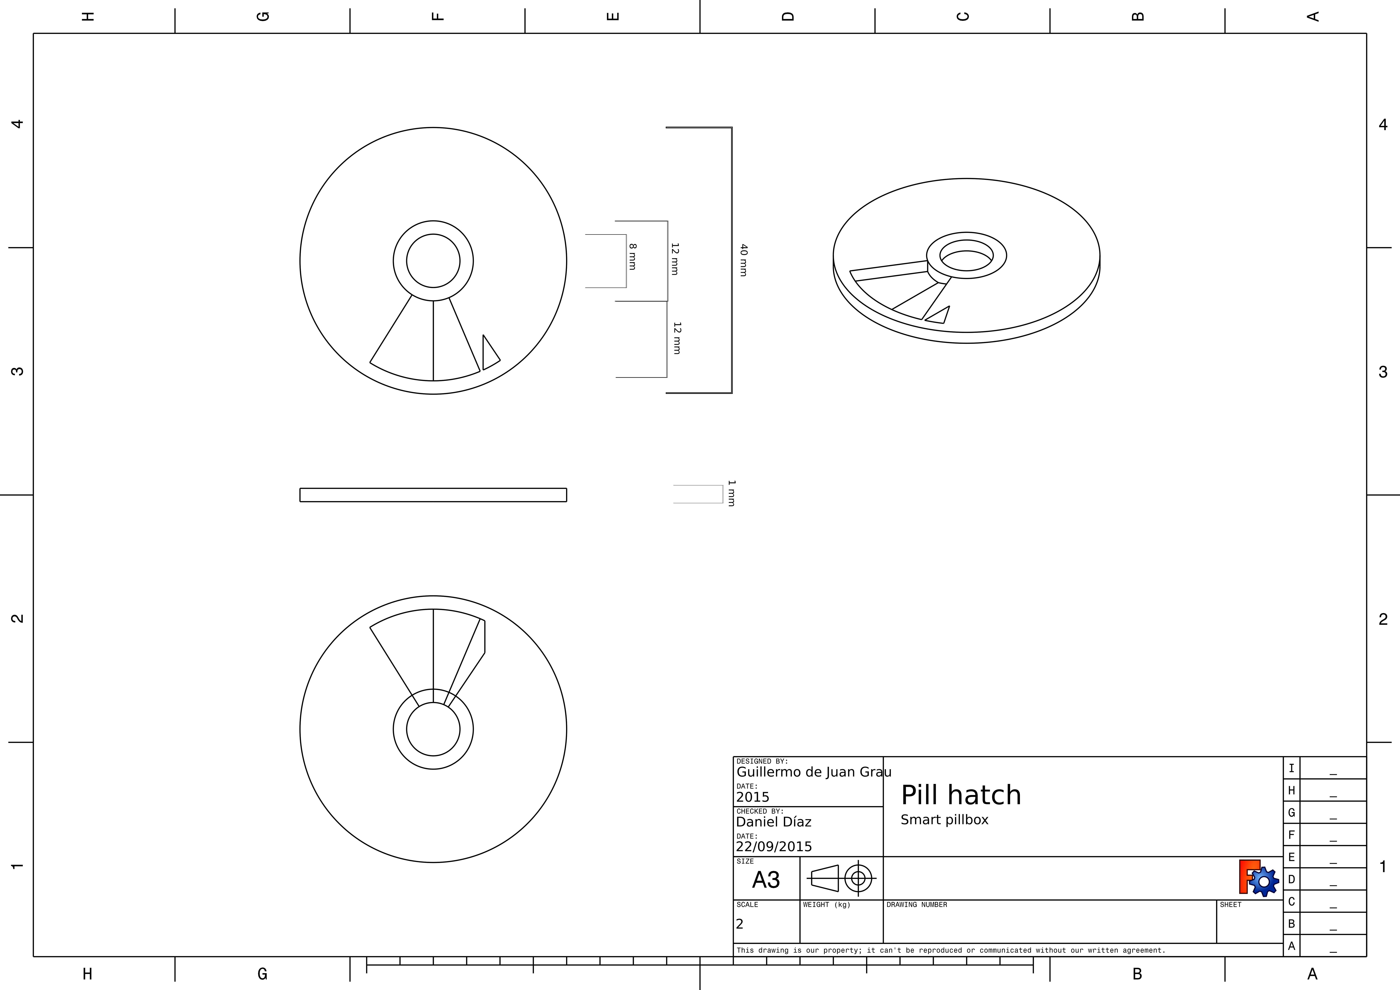
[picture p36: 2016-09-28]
Body/Measured blueprints/Pill hatch2.png

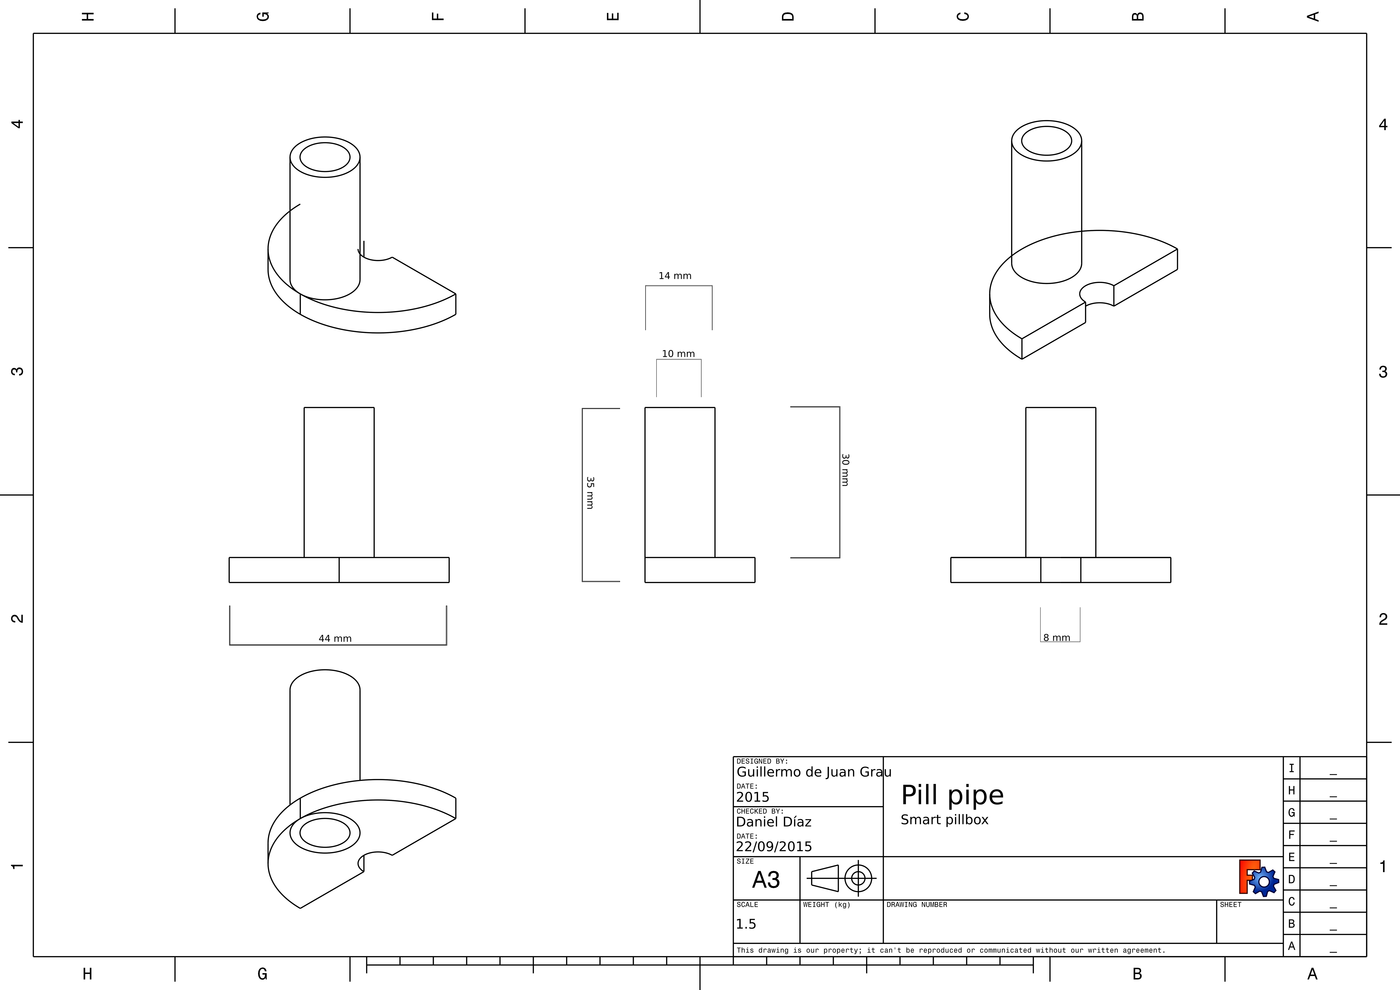
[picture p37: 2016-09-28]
Body/Measured blueprints/Pill pipe2.png

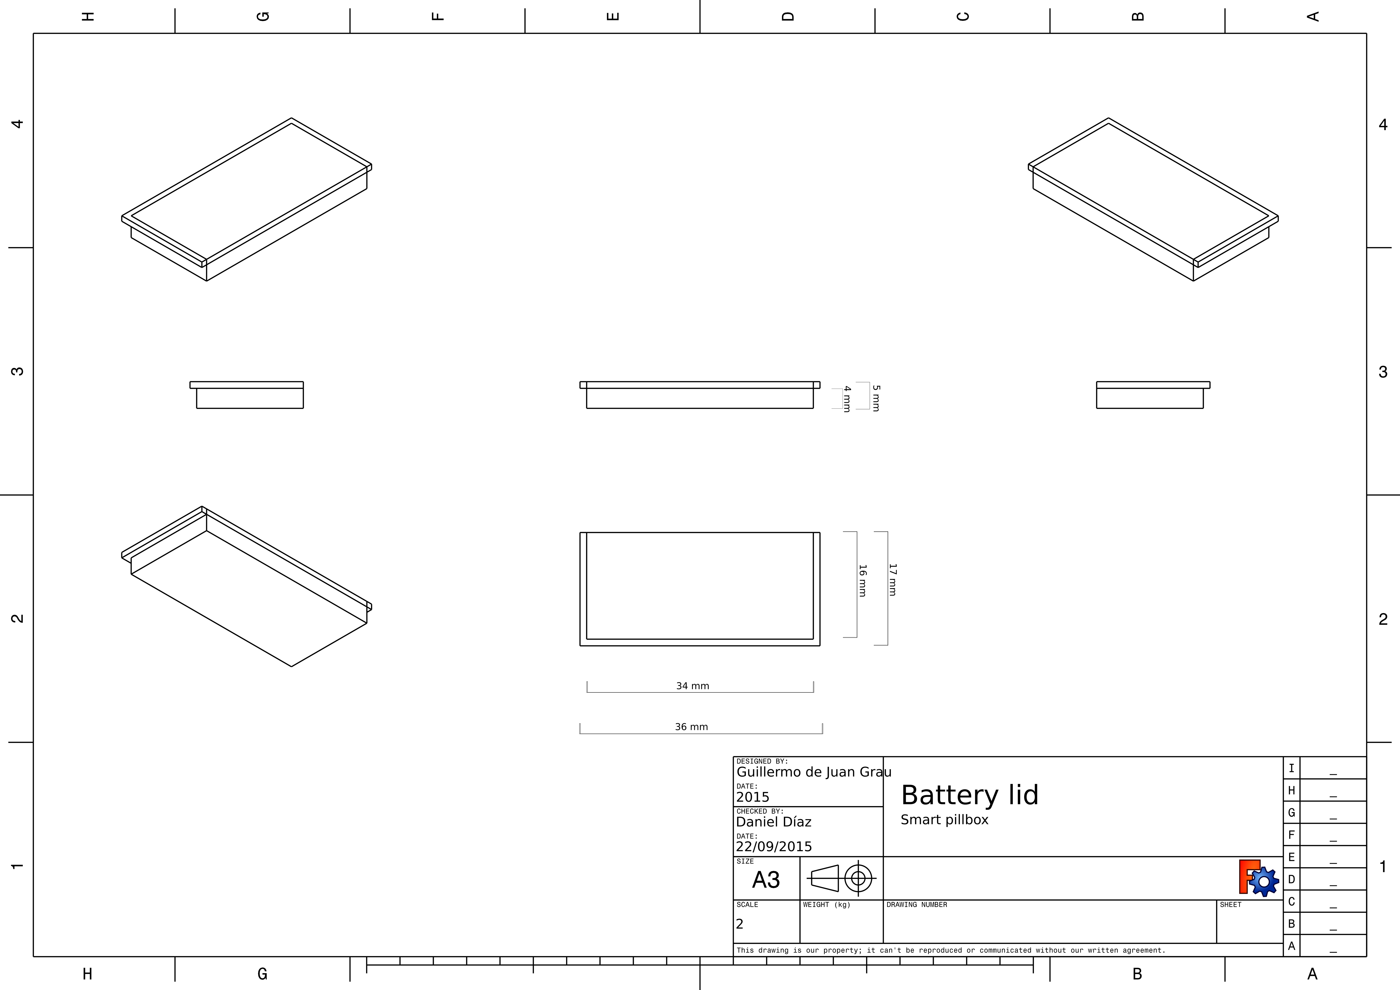
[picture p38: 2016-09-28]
Body/Measured blueprints/Battery lid2.png

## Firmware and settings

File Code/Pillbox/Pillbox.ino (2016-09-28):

/***********************/
/*Constant definitions*/
/*********************/
#define dispButton 2
#define switchBT 3
#define dispLed 4
#define speaker 9


/*******************/
/*Libraries needed*/
/*****************/
#include <EEPROM.h>
#include <Servo.h>
#include <Wire.h>
#include "RTClib.h"


Servo upperServo; //Upper servo declaration
Servo lowerServo; //Lower servo declaration
RTC_DS1307 RTC; //Real-Time Clock module declaration
long debouncing_time = 15; //Debouncing Time in Milliseconds
volatile unsigned long last_micros; //Variable needed for the button debounce
int dispensingFlag = 0; //Flag to signal if a pill is requested by the user
DateTime now;
int day = 0;
int hour = 0;
int minute = 0;

//Array where the next dose to be dispensed will be stored
byte actualDose[4] = {255, 255, 255, 255};

int command = 0;

//Array where the dose timetable will be loaded during runtime
byte doses[120][4];

//Array where the logs will be kept
byte logs[120][4];
unsigned long timesinceon;


/**********************************/
/*Different upper servo positions*/
/********************************/
int pillAdisppos = 0; //Pill A dispensing position
int pillBdisppos = 0;//Pill B dispensing position
int pillCdisppos = 0;//Pill C dispensing position
int defaultpillstoragepos = 0;//Default pill storage position
int pillAloadpos = 0;//Pill A loading position
int pillBloadpos = 0;//Pill B loading position
int pillCloadpos = 0;//Pill C loading position


/**********************************/
/*Different lower servo positions*/
/********************************/
int loadpos = 0;//Pill chamber loading position
int releasepos = 0;//Pill chamber releasing position
int finishedrefilling = 120;

void setup() {
  pinMode(dispButton, INPUT);
  pinMode(switchBT, INPUT);
  pinMode(dispLed, OUTPUT);
  pinMode(speaker, OUTPUT);
  upperServo.attach(5);//Attach upper servo to pin 5
  lowerServo.attach(6);//Attach lower servo to pin 6
  digitalWrite(dispLed, LOW);
  attachInterrupt(2, debounceInterrupt, RISING);//Attach an interrupt to pin 2
  Serial.begin(9600);
  Wire.begin();
  RTC.begin();
  loadTimetable(doses);//Load the doses timetable from the EEPROM memory into the doses array
  now = RTC.now();//The actual date is gathered from the RTC module
  day = now.dayOfTheWeek();

  int i = 0;
 while (doses[i][0] != day) {
    doses[i][0] = 255;
    doses[i][1] = 255;
    doses[i][2] = 255;
    doses[i][3] = 255;

  }

}
void loop() {
  if (digitalRead(switchBT) == HIGH) {//Check if the Bluetooth switch is active
    if (Serial.available() > 0) {//Check if there is Serial data available
      command = Serial.read(); //Read the command sent by the device to the pillbox
      switch (command) {
        case 1: //Case 1 corresponds to sending the timetable to the device
          Serial.write("Sending the timetable now.");
          byte complete_timetable[256][4];//An array where the complete timetable will be loaded
          loadTimetable(complete_timetable);//Load the timetable from memory into the array
          for (int i = 0; i < 256; i++) {
            for (int j = 0; j < 4; j++) {
              Serial.write(complete_timetable[i][j]);//Writes the array in order to the device
            }
          }
          sendClosingSequence();
          break;
        case 2: //Case 2 corresponds to the device sending a new timetable for the pillbox
          Serial.write("Updating timetable procedure started.");
          byte new_timetable[256][4];
          for (int i = 0; i < 256; i++) {
            for (int j = 0; j < 4; j++) {
              new_timetable[i][j] = Serial.read(); //The new timetable is read byte by byte
            }
          }
          overwrite_timetable(new_timetable);//Overwrite the EEPROM memory with the new timetable
          loadTimetable(doses);//Load the new timetable from the recently overwritten EEPROM memory into the doses array
          sendConfirmationSequence();//Send a sequence so that the device knows the transference has been correctly done
          sendClosingSequence();
          break;
        case 3: //Case 3 sends how much time the device has been powered on for battery saving causes
          timesinceon = millis();
          Serial.write(timesinceon);
          sendClosingSequence();
          break;
        case 4: //Case 4 sends the logs of the times at which the pills were actually taken
          for (int i = 0; i < 256; i++) {
            for (int j = 0; j < 4; j++) {
              Serial.write(logs[i][j]);
            }
          }
          sendClosingSequence();

        case 5: //Case 5 activates the refilling sequence
          Serial.write("Refilling sequence activated.");
          int movement;
          //The device sends a number, this number will either be ond of the pill refilling position or a number interpreted as a command to stop the refilling sequence
          movement = Serial.read();      
          //While the number sent is not the one which stops the refilling sequence the pill storage will rotate to the sent positiom
          while (movement != finishedrefilling) {
            upperServo.write(movement);
            delay(1000);
            movement = Serial.read();
          }
          upperServo.write(defaultpillstoragepos);//After finishing the refilling sequence the pill storage will be rotated to its default positions
          delay(1000);
          sendClosingSequence();
          break;
        default:
          sendClosingSequence();
          break;
      }
    } else {
    }
  } else {
    now = RTC.now();//The actual date is gathered from the RTC module
    day = now.dayOfTheWeek();
    hour = now.hour();
    minute = now.minute();
    loadNextDose();//The next dose in line will be loaded into the actualDose variable.
    if (day == actualDose[0] && hour >= actualDose[1] && minute >= actualDose[2]) { //Checks the time of the next dose with the actual time
      if (minute - actualDose[3] < 5 ) {//If the next pill was to be taken less than five minutes ago visual and acoustic signals are sent
        digitalWrite(dispLed, HIGH);
        alarm();
      } else {
        digitalWrite(dispLed, HIGH);//Only visual notifications are activated if the pill had to be taken more than five minutes ago
      }
    }
    if (dispensingFlag == 1) {//If the flag to dispense a pill was pressed
      int pill = actualDose[3];
      dispensePill(actualDose[3]);//The dispensing procedure is activated for the pill type which has to be taken
      for (int i = 0; i < 256; i++) {//A for loop is created to log the pill dose time
        if (logs[i][0] == 255) {
          logs[i][0] = day;
          logs[i][1] = hour;
          logs[i][2] = minute;
          logs[i][3] = pill;
        }
      }
    }
  }
}

/***********************************************************/
/*loadTimetable: */
/*This function recieves an array of bytes as an argument*/
/*and loads the dose timetable from the EEPROM memory */
/*into the array */
/******************************************************/
void loadTimetable(byte array_to_fill[][4]) {
  int address = 0;
  for (int i = 0; i < 256; i++) {
    for (int j = 0; j < 4; j++) {
      array_to_fill[i][j] = EEPROM.read(address);
      address++;
    }
  }
}
/***************************************************************/
/*debounceInterrupt: */
/*The method which prevents the dispensing button press from */
/*debouncing and then activates the flag to dispense a pill.*/
/***********************************************************/
void debounceInterrupt() {
  if ((long)(micros() - last_micros) >= debouncing_time * 1000) {
    dispensingFlag = 1;
    last_micros = micros();
  }
}
/****************************************************************/
/*loadNextDose: */
/*This function retrieves the next dose to be taken from */
/*the doses array and stores it into the actualDose variable.*/
/************************************************************/
void loadNextDose() {
  int dosetocompare;
  for (int i = 0; i < 256; i++) {
    dosetocompare = (int)doses[i];
    if (dosetocompare != 255) {
      for (int j = 0; j < 4; j++) {
        actualDose[j] = doses[i][j];
        doses[i][j] = 255;
      }
      break; //para salirnos del for loop
    }
  }
}
/*****************************************************************************/
/*dispensePill: */
/*This function starts the pill dispensing procedure to */
/*dispense the pill type which is notified with the function's argument */
/*and rotates the servos in turn to dispense the pill */
/************************************************************************/
void dispensePill(int typeOfPill) {
  if (typeOfPill != 255) { //Esto comprueba que no haya fallos o que la pildora cargada sea correcta
    upperServo.write(typeOfPill);
    delay(200);
    lowerServo.write(loadpos); //posicion de carga
    delay(200);
    upperServo.write(defaultpillstoragepos);
    delay(200);
    lowerServo.write(releasepos);
    delay(200);
    digitalWrite(dispLed, LOW);
  }
}
/***********************************************************************/
/*sendConfirmationSequence: */
/*This function sends to the other device a */
/*preestablished confirmation sequence to indicate the new timetable*/
/*has been correctly received */
/******************************************************************/
void sendConfirmationSequence() {
  byte confirmationsequence[5] = {200, 200, 200};
  int i = 0;
  for (int i = 0; i < 3; i++)
    Serial.write(confirmationsequence[i]);
}
/************************************************************/
/*sendClosingSequence: */
/*This function sends to the other device a */
/*preestablished closing sequence to indicate the correct*/
/*termination of the bluetooth command */
/*******************************************************/
void sendClosingSequence() {
  byte closingsequence[5] = {255, 254, 255};
  int i = 0;
  for (int i = 0; i < 3; i++)
    Serial.write(closingsequence[i]);
}
/***********************************************************/
/*overwrite_timetable: */
/*This function recieves an array of bytes as an argument*/
/*and overwrites the timetable stored in the EEPROM */
/*memory with the one in the array */
/******************************************************/
void overwrite_timetable(byte new_timetable[][4]) {
  int address = 0;
  for (int i = 0; i < 256; i++) {
    for (int j = 0; j < 4; j++) {
      EEPROM.put(new_timetable[i][j], address);
      address++;
    }
  }
}
/******************************************************/
/*alarm: */
/*This function emits an alarm through the speaker */
/*to signal the acoustic notification of a new dose*/
/**************************************************/
void alarm() {
  tone(speaker, 440, 2000);
}
